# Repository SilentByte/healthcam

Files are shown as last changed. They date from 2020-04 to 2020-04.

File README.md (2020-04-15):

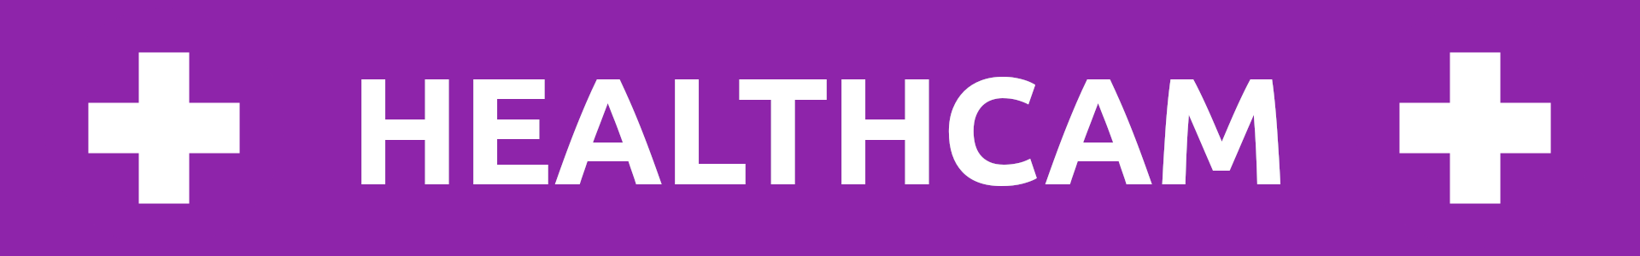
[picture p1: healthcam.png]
HealthCam


 &nbsp;
 &nbsp;


# HealthCam

In an effort to help with the currently ongoing COVID-19 health crisis, we have developed [HealthCam (healthcam.silentbyte.com)](https://www.healthcam.silentbyte.com/), a system based on the Raspberry Pi Camera and utilizing the [PPE Detector for Laboratory Safety](https://aws.amazon.com/marketplace/pp/prodview-b53upp27dnmzq) model provided by VITech Lab, which provides predictions for whether a person is wearing a mask or not. With this information, the system is able to automatically restrict door-access to sterile areas for people not wearing a mask in order to prevent the spread of infections.

Our submission contains two major components: the actual Raspberry Pi Camera with a door lock and the accompanying website to give
administrators access to manually flag detections as incorrect, and to view history of compliance, violation and manual
override events.

## AWS Services Used

| Service | Usage |
|---|---|
| Greengrass | Remote code deployment onto Raspberry Pi |
| API Gateway | Framework to publish and manage API |
| Lambda | Serverless functions to perform API actions|
| Amplify | Framework to build web applications |
| S3 | Object storage |
| RDS | Hosting of a PostgresSQL database |
| IAM | Management of AWS Permissions |
| Sagemaker Models Marketplace | Model for Mask detection |

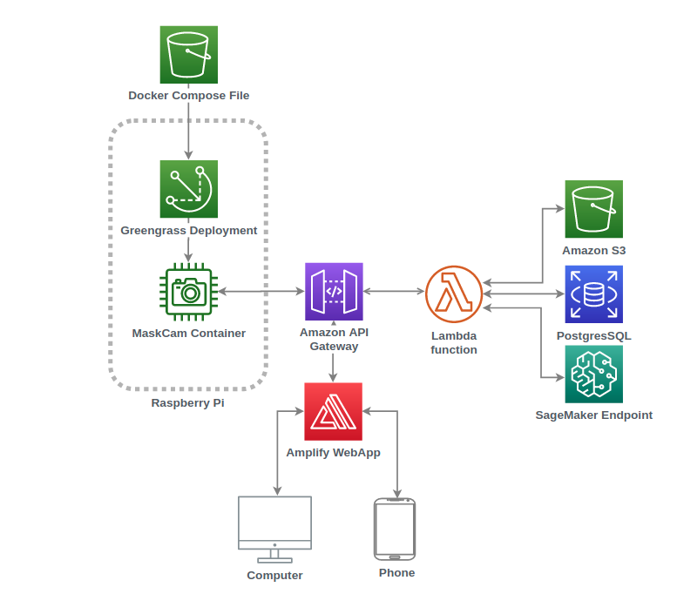
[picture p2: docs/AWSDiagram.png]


## Website
The website is powered by AWS Amplify and Vue/Vuetify, with all API calls made to AWS API Gateway. This website gives administrators the ability to manually flag detections as incorrect and view a history of compliance, violation and manual override events.

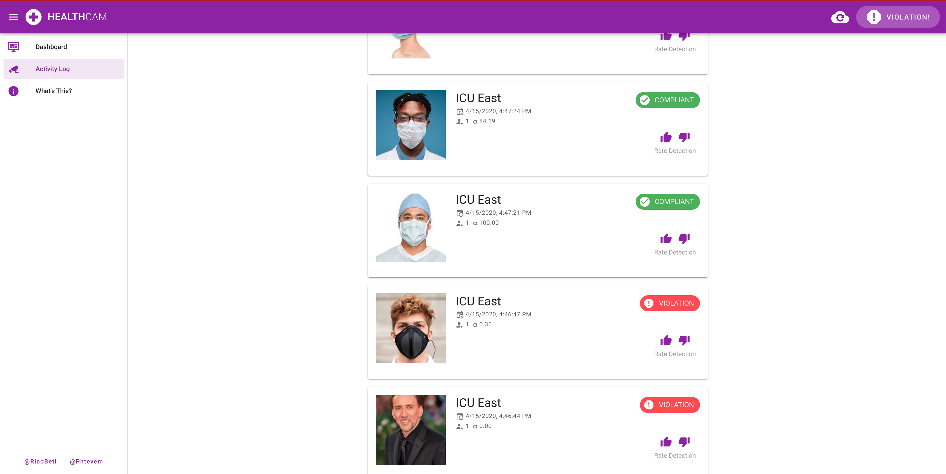
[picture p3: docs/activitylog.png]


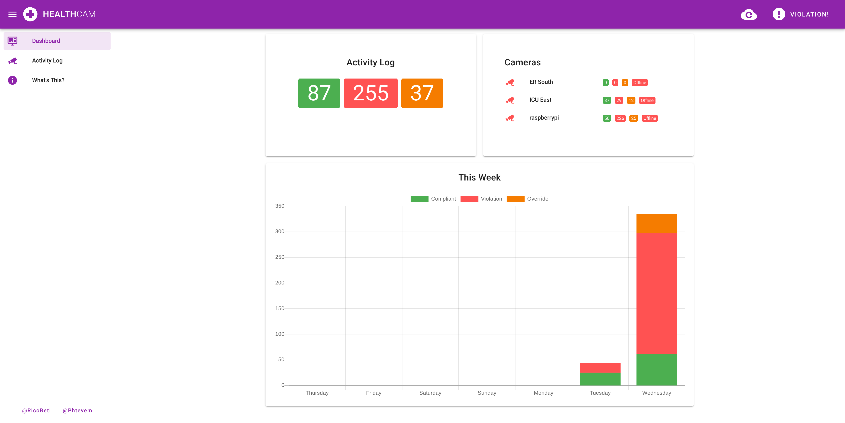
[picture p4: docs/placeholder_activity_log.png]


When the Rasbperry Pi detects movement in the frame, it sends an image along with some metadata to an API gateway endpoint.
A lambda function then picks this up, and first queries a Sagemaker endpoint created with the
[PPE Detector for Laboratory Safety](https://aws.amazon.com/marketplace/pp/prodview-b53upp27dnmzq).
The endpoint then returns information about the number of people in frame, the probability that each item is a person,
and the probability that they're wearing a mask. If there are people in the frame, then we take the lowest mask detected
probability, compare it to a user defined minimum probability to determine whether it's compliant or not and upload image
to a S3 bucket, a reference to where that image is along with the probability and number of people in frame to an RDS instance. Finally the Lambda sends a response back for whether the door should be opened or not. We have implemented a manual override button to open the door for emergency situations and in case of a false detection to guarantee that health works can continue to operate effectively and efficiently.

## Raspberry Pi
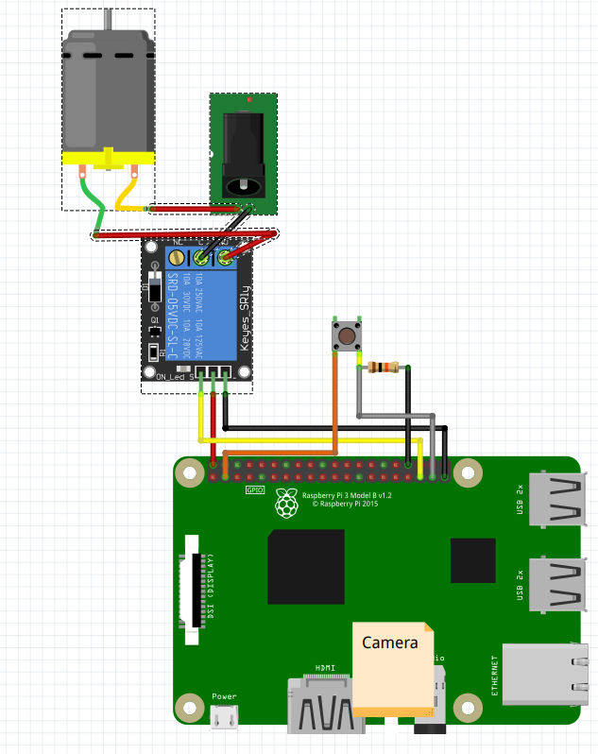
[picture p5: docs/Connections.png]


The Raspberry Pi system runs AWS Greengrass core. This allows the remote pushing of code and configurations through the AWS Greengrass Docker connector.
The main "Program" is installed as a python package and continually monitors for a percentage of pixels that have changed
by some user defined percentage. If this threshold has exceded then it will send the image it has captured through to
an AWS API Gateway endpoint, which will then do analysis on the image using the
[PPE Detector for Laboratory Safety](https://aws.amazon.com/marketplace/pp/prodview-b53upp27dnmzq) model, to determine
whether everyone in frame is wearing a mask.

If they are wearing a mask, then the Raspberry Pi Turns a GPIO pin connected to a relay to HIGH, which will actuate the
locking mechanism.

In the event of an emergency or false detection, there is a manual override button which will trigger an interrupt, immediately opening the
door, recording a picture and tagging the event as "override".

### Bill of Materials
| Item | Description |
| ---|---|
| [USB-C 5V 3A Power Supply](https://www.ebay.com.au/itm/Raspberry-Pi-4-4B-Power-Supply-Adapter-ON-OFF-Switch-USB-C-5V-3A-US-EU-Plug/303278828464) | Power for the Raspberry Pi |
| [12V 1A Power Supply](https://www.ebay.com.au/itm/AC-100-240V-Converter-Adapter-DC-12V-1A-12W-Power-Supply-AU-Plug-Wall-Charger/401648202115) | Power for the Lock Mechanism |
| [Electronic Latch Lock](https://www.ebay.com.au/itm/Electronic-Latch-Lock-Catch-Door-12V-Electro-magnet-Release-Solenoid-Slant-Slug/163889580407)| Lock Mechanism for Door |
| [5V relay](https://www.ebay.com.au/p/902676901) | Relay to isolate the lock power from the Pi|
| [Pi Camera V2](https://www.ebay.com.au/itm/Raspberry-Pi-Camera-Board-V2/323833141585) | Camera |
| [Dupont Line](https://www.ebay.com.au/itm/10-20-30CM-40PCS-Pin-Dupont-Wire-Line-Ribbon-M-F-M-M-F-F-Jumper-Cables-Arduino/274194461478) | Wiring |
| [Button](https://www.ebay.com.au/itm/10pcs-6x6x4-9mm-4pin-G89-Tactile-Push-Button-Micro-Switch-Self-Reset-Dip-Press/132693965284) | Press button for manual override of system |
| [10KΩ Resistor](https://www.ebay.com.au/itm/10pcs-1-4-Watt-0-25W-Metal-Film-Resistors-1-Full-Range-of-Values-0-to-10M/192581889373) | Pull down resistor for button |

## Setup

We've written extensive documentation on how to setup the aws resources and raspberry pi requirements to run this.

1. [Create Sagemaker Endpoint](setup/1_create_endpoint.md)

2. [Setup Frontend](setup/2_frontend.md)

3. [Setup Pi](setup/3_pi_setup.md)

## Challenges we ran into

### GreenGrass Setup
We wanted to drive our development and infrastructure without having to click through into the AWS UI to try to learn
how to better use the CLI and AWS SDKs. Because we hadn't used much Greengrass in the past it took us a while to properly
setup a Greengrass core and drive deployments without using the AWS UI. We'd recommend checking out this
[article](https://devopstar.com/2019/10/07/aws-iot-greengrass-cloudformation-raspberry-pi) if you're attempting greengrass and Raspberry Pi.
Unfortunately due to time constraints and last minute changes, one of the dependencies we introduced didn't work well with our docker container, so we had to deploy via Pip instead.

### IAM
We don't work with AWS a lot and we wanted to avoid our bad behaviours of the past with allow *, so learning how to properly apply the required AWS policies to roles specific to their task was an interesting experience. We've identified a lot of cases where we could have done a lot better, so hopefully we'll fix those up.

### OpenCV and Raspberry Pi
Some changes to OpenCV (used for detecting image differences) in November broke a few packages. Thankfully
[Adrian Rosebrock](https://www.pyimagesearch.com/2019/09/16/install-opencv-4-on-raspberry-pi-4-and-raspbian-buster/)
has updated his blog with steps around this. In retrospect given the problems we had, it would probably have been worth
doing the pixel change detection in numpy instead of using such a heavy library to do it for us.

### Models Limitations
Currently, the SageMaker model seems to have a limitation in that it doesn't properly detect non-white/blue masks.

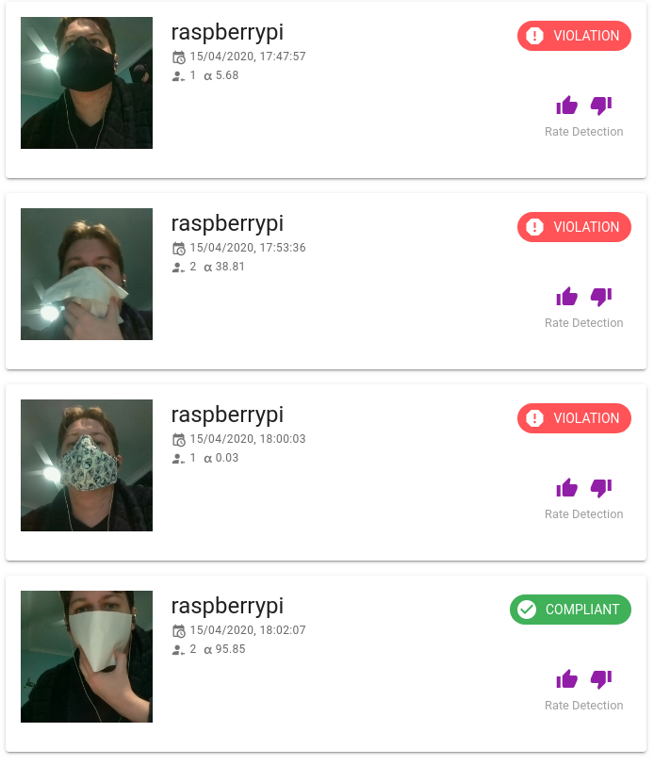
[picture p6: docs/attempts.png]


## What We Learnt

This hackathon gave us the chance to once again dive into Amazon Web Services. New services for us this time were AWS IoT Greengrass and AWS Amplify, which are now part of our toolbox.

## What's Next
### Authentication
Currently there is no Authentication on the API gateway or website. This is something that's probably required if anyone
is going to use this, so it would be well worth us putting in the effort to get this in. We would probably want to use
AWS Cognitio with Federated Identities to do manage credentials.

### Cloudformation Deployments
Because we used two different frameworks (Serverless Framework and AWS Amplify) we didn't really have a single deployment pipeline.
Ideally we'd fully embrace Infrastructure as a Service and use Cloudformation to manage all of our cloud resources.

### Proper Deployment Pipleine (CICD)
One of the things that slowed us down a bit was the lack of a proper deployment pipeline which occasionally slowed us down:

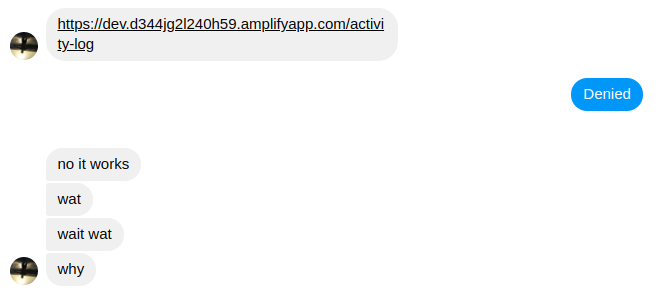
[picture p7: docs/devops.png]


We would probably want to implement proper Continuous Integration/Continuous Deployment to avoid us
having to push code manually and to make sure that we have some automated tests running against our code once deployed to AWS.

### Proper Bootstrap Script for Raspberry Pi
Currently the setup of the Raspberry Pi and Greengrass is a bit more complicated than it needs to be. Based on the steps,
it should be easy enough to set up a proper bootstrap script to setup the pi ready for greengrass deployments.

## Thanks
There were a few resources that we found invaluable while we were making this
* [Setting up Greengrass on a Raspberry Pi](https://devopstar.com/2019/10/07/aws-iot-greengrass-cloudformation-raspberry-pi) was a great into to Greengrass.
* [Accessing the Raspberry Pi Camera](https://www.pyimagesearch.com/2015/03/30/accessing-the-raspberry-pi-camera-with-opencv-and-python/)
had some useful tips on how to poll the Pi Camera a lot faster than I was previously polling it.
* [Install OpenCV4 on Raspberry Pi](https://www.pyimagesearch.com/2019/09/16/install-opencv-4-on-raspberry-pi-4-and-raspbian-buster/)
* [Launch RDS with AWS CLI](https://www.mydatahack.com/how-to-launch-postgres-rds-with-aws-command-line-interface-cli/)
* [raspi-config noint commands](https://github.com/l10n-tw/rc_gui/blob/master/src/rc_gui.c#L50-L100) very useful for enabling things via cli
* [AWS Docker Connector](https://docs.aws.amazon.com/greengrass/latest/developerguide/docker-app-connector.html) information on the greengrass docker connector

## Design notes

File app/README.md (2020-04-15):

HealthCam

 &nbsp;
 &nbsp;


# HealthCam App

This part of the repository is representing the front-end of the HealthCam app and is based on Vue and Vuetify.

## Development

In order to start development on this project, follow the steps below:

*   Ensure that the AWS Lambda-based back-end service is running locally on port 8888. You can find instructions in the `./lambdas` folder in this repository.

*   Install app dependencies:
    ```bash
    $ cd app
    $ npm install
    ```

*   Start app in development mode:
    ```bash
    $ npm run dev
    ```

    At this point, the app should have been bundled and a development server should have been started on port 8080.

## Deployment

This project is powered by [AWS Amplify](https://aws-amplify.github.io/) and requires you to sign up for an AWS account if you choose to deploy using that service.

*   Ensure that the AWS Lambda-based back-end has been deployed. You can find instructions in the `./lambdas` folder in this repository.

*   Create the file `.env.development.local` in the `./app/` folder and set the endpoint URL to the base URL to which the Lambda service has been deployed:

    ```
    VUE_APP_API_URL=https://your-lambda-url.execute-api.us-east-1.amazonaws.com/dev
    ```

*   Configure your AWS Amplify project:
    ```bash
    $ cd app
    $ npm install -g @aws-amplify/cli
    $ amplify configure
    ```

*   Publish the HealthCam app on AWS Amplify:
    ```bash
    $ amplify publish
    ```

If the deployment has been successful, a publicly accessible URL will be displayed and HealthCam is now up and running. :-)

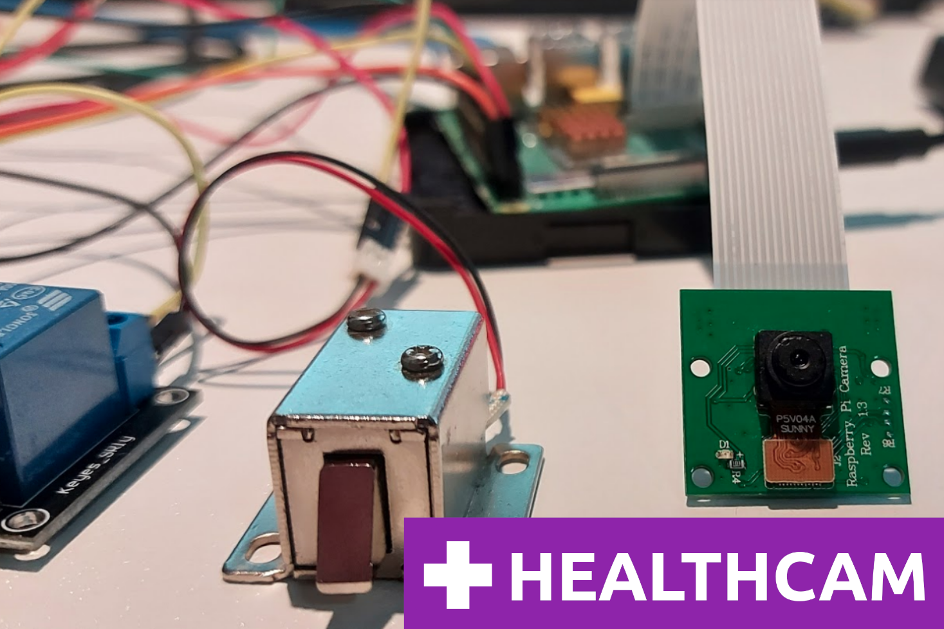
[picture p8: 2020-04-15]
docs/project.png

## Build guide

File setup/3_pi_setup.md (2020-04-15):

# Set up Pi
[Download Raspbian Buster lite](https://downloads.raspberrypi.org/raspbian_lite_latest) and extract it

Use [Etcher](https://www.balena.io/etcher/) to install the Rasbpian ISO to your SD Card.

On your SD card go to ```boot``` and add a new file called ```ssh```. This will enable SSH on boot.

You should now be able to put your SD card 

Check that your raspberry Pi is online with ```ping raspberrypi.local```
```
PING raspberrypi.local (192.168.0.167) 56(84) bytes of data.
64 bytes from raspberrypi.modem (192.168.0.167): icmp_seq=1 ttl=64 time=0.889 m
```

SSH into the Raspberry Pi

```
# Enable GPIO and Camera
sudo apt-get update
sudo apt-get install pigpio -y
sudo raspi-config nonint do_camera 1
sudo raspi-config nonint do_rgpio 1
# Install docker
sudo apt install docker docker-compose -y
# Setup docker group for current user and green grass user
sudo adduser -m ggc_user
sudo addgroup --system ggc_group
sudo groupadd docker
sudo usermod -aG docker pi
sudo usermod -aG docker ggc_user
# setup opencv (for devel purposes).
sudo apt install libtiff-dev libjpeg8-dev libpng12-dev build-essential  -y
sudo apt install python3-pyqt5 libqtgui4 libjasper-dev libatlas-base-dev libatlas-base-dev libgtk2.0-dev libtbb-dev qt5-default -y
sudo apt install python3-opencv -y
```

Install the MaskCam package
```
git clone git@github.com:SilentByte/healthcam.git
cd healthcam/Picode
pip3 install -r requirements.txt
pip3 install -e .
```
You should now be able to run ```MaskCam``` to access settings 
```zsh
pi@raspberrypi:~ $ MaskCam --help
Usage: MaskCam [OPTIONS] COMMAND [ARGS]...

Options:
  --camera_number INTEGER       Raspberry Pi camera number according to https:
                                //picamera.readthedocs.io/en/release-1.13/api_
                                camera.html#picamera, Default: 0

  --camera_invert BOOLEAN       Vertical invert camera, Default: True
  --device_name TEXT            Device Name, Default: raspberrypi
  --minimum_difference INTEGER  Minimum difference between frames to send,
                                Default: 50

  --api_gateway TEXT            AWS API Gateway Endpoint, Default:
                                https://m5k4jhx1ka.execute-api.us-
                                east-1.amazonaws.com/dev/

  -v, --verbose                 Verbosity. More v, more verbose. Eg -vvv
  --door_button INTEGER         Pin that the override button is connected to,
                                Default: 37

  --door_pin INTEGER            Pin the door latch is connected to, Default:
                                35

  --opening_time INTEGER        Time to open door in seconds., Default: 5
  --help                        Show this message and exit.

Commands:
  to_aws
  to_file
  to_stdout
```
For most cases if you run ```MaskCam --api_gateway {YOUR GATWAY URL} to_aws``` you should be fine.

#Setup Greengrass
# Setup Roles
## Bootstrap Role
Create the "Bootstrap" role which will install your greengrass components onto your raspberry pi.

get your ARN with ```aws iam get-role --role-name Greengrass_ServiceRole ```
```
aws greengrass associate-service-role-to-account --role-arn {YOUR_ROLE} --region us-east-1

```
Create a "boostrap" user that will be creating your greengrass core deployment
```
aws iam create-user --user-name bootstrapuser
aws iam create-access-key --user-name bootstrapuser
aws iam attach-user-policy --user-name bootstrapuser --policy-arn arn:aws:iam::aws:policy/AWSGreengrassFullAccess
aws iam attach-user-policy --user-name bootstrapuser --policy-arn arn:aws:iam::aws:policy/AWSIoTConfigAccess
aws iam attach-user-policy --user-name bootstrapuser --policy-arn arn:aws:iam::aws:policy/IAMFullAccess
```

## Greengrass Service Role
Create your Greengrass Service Role to allow your greengrass group to run.
Check if you have a previous service role
```
aws greengrass get-service-role-for-account --region us-east-1
```
Diasassociate it
```
aws greengrass disassociate-service-role-from-account --region region
```
Give your role the required permissions
```
aws iam create-role --role-name Greengrass_ServiceRole --assume-role-policy-document '{
  "Version": "2012-10-17",
  "Statement": [
    {
      "Effect": "Allow",
      "Principal": {
        "Service": "greengrass.amazonaws.com"
      },
      "Action": "sts:AssumeRole"
    }
  ]
}'
aws iam attach-role-policy --role-name Greengrass_ServiceRole --policy-arn arn:aws:iam::aws:policy/service-role/AWSGreengrassResourceAccessRolePolicy
```
Download greengrass setup
```
wget -q -O ./gg-device-setup-latest.sh https://d1onfpft10uf5o.cloudfront.net/greengrass-device-setup/downloads/gg-device-setup-latest.sh && chmod +x ./gg-device-setup-latest.sh
```
Input the aws-access-key-id and aws-secret-access-key from ```aws iam create-access-key --user-name bootstrapuser```. This will createa a group-name and core-name with the serial number of your raspberry pi.
```
sudo ./gg-device-setup-latest.sh bootstrap-greengrass \
--aws-access-key-id {} \
--aws-secret-access-key {} \
--region us-east-1 \
--group-name $(cat /proc/cpuinfo | grep Serial | cut -d ' ' -f 2) \
--core-name $(cat /proc/cpuinfo | grep Serial | cut -d ' ' -f 2)

```

```
[GreengrassDeviceSetup] A reboot is required to make cgroups configuration change effective.
You must reboot your device manually and then restart GreengrassDeviceSetup.
```

```sudo reboot```
re run the previous ```./gg-device-setup-latest.sh``` command. This time you'll get
```
Do you want to reuse the configuration from your previous session? Enter 'yes' to reuse the configuration or 'no' to restart the installation.
```
yes

```
You can now use AWS IoT Console to manage your Greengrass group.
```

attach the service role to your docker

```
aws greengrass list-groups
```
get your group name and attach your service role with it
```
get your ARN with ```aws iam get-role --role-name Greengrass_ServiceRole ```
```
Associate this role with your greengrass group
```
aws greengrass associate-role-to-group --group-id {YOUR_GROUP_ID} --role-arn {YOUR_ROLE_ARN}
```
Confirm with
```
aws greengrass get-associated-role --group-id {YOUR_GROUP_ID}
```

# Deploy your container
Replace YOUR_BUCKET_NAME and YOUR_DOCKER_COMPOSE_FILE_NAME with what you created in step 1.
```
aws greengrass create-connector-definition --name MyGreengrassConnectors --initial-version '{
    "Connectors": [
        {
            "Id": "MyDockerAppplicationDeploymentConnector",
            "ConnectorArn": "arn:aws:greengrass:region::/connectors/DockerApplicationDeployment/versions/2",
            "Parameters": {
                "DockerComposeFileS3Bucket": "{YOUR_BUCKET_NAME}",
                "DockerComposeFileS3Key": "{YOUR_DOCKER_COMPOSE_FILE_NAME}",
                "DockerComposeFileDestinationPath": "/home/ggc_user",
                "ForceDeploy": "True"
            }
        }
    ]
}'
```
you should now be able to create a new deployment via the AWS console

# References
[Enable SSH on boot](https://www.raspberrypi.org/forums/viewtopic.php?t=129727)

[raspi-config noint commands](https://github.com/l10n-tw/rc_gui/blob/master/src/rc_gui.c#L50-L100)

[Greengrass quick setup](https://docs.aws.amazon.com/greengrass/latest/developerguide/quick-start.html)

[Connector](https://docs.aws.amazon.com/greengrass/latest/developerguide/docker-app-connector.html)
[Install OpenCV4](https://www.learnopencv.com/install-opencv-4-on-raspberry-pi/)

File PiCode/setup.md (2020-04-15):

```
model_package=arn:aws:sagemaker:us-east-1:865070037744:model-package/sassy-atermis-05-693a26662ad851a0e47bf8146e940526
aws iam list-roles --query 'Roles[?AssumeRolePolicyDocument.Statement[?Principal.Service==`sagemaker.amazonaws.com`]].{Arn:Arn,RoleName:RoleName,Principal:AssumeRolePolicyDocument.Statement[0].Principal.Service}'
aws iam get-role --query 'Role.{Arn:Arn}' --role-name <role-name>
execution_role_arn=<iam-role-arn>
instance_type=ml.p2.xlarge
supported_instance_types=(ml.p2.xlarge)

aws sagemaker create-model --model-name sample-model-51119791-78EE-457C-AA7F-679C5CE281DE-1 --execution-role-arn ${execution_role_arn} --primary-container ModelPackageName=${model_package} --enable-network-isolation --region us-east-1
aws sagemaker create-endpoint-config --endpoint-config-name sample-endpointcfg-51119791-78EE-457C-AA7F-679C5CE281DE-1 --production-variants VariantName=variant-1,ModelName=sample-model-51119791-78EE-457C-AA7F-679C5CE281DE-1,InstanceType=${instance_type},InitialInstanceCount=1 --region us-east-1
aws sagemaker create-endpoint --endpoint-name sample-endpoint-51119791-78EE-457C-AA7F-679C5CE281DE-1 --endpoint-config-name sample-endpointcfg-51119791-78EE-457C-AA7F-679C5CE281DE-1 --region us-east-1
aws sagemaker describe-endpoint --endpoint-name sample-endpoint-51119791-78EE-457C-AA7F-679C5CE281DE-1 --region us-east-1

```

```
sudo apt install python3 python3-pip
pip3 install -r requirements.txt
sudo apt-get install python-opencv
pip install opencv-contrib-python==4.1.0.25
sudo apt-get install python-opencv
sudo apt install libatlas3-base libwebp6 libtiff5 libjasper1 libilmbase12 libopenexr22 libilmbase12 libgstreamer1.0-0 libavcodec57 libavformat57 libavutil55 libswscale4 libqtgui4 libqt4-test libqtcore4
sudo apt-get install libjpeg-dev libtiff5-dev libjasper-dev libpng12-dev -y
sudo apt install libqt4-test

sudo apt-get install libatlas-base-dev 

sudo apt-get install libjasper-dev 

sudo apt-get install libqtgui4 

sudo apt-get install python3-pyqt5 

sudo apt install libqt4-test

sudo apt install python3-pyqt5 libqtgui4 libjasper-dev libatlas-base-dev -y
sudo apt install python3-opencv -y

sudo apt-get install libavcodec-dev libavformat-dev libswscale-dev libv4l-dev -y
sudo apt-get install libxvidcore-dev libx264-dev -y
sudo apt-get install libgtk2.0-dev libgtk-3-dev -y
sudo apt-get install libatlas-base-dev gfortran -y
sudo apt-get install libqtgui4 python3-pyqt5 libjasper-dev libatlas-base-dev
sudo apt-get install 

```
# Sagemaker
```
https://aws.amazon.com/marketplace/pp/prodview-3dr4kos6pq5cq?ref_=ml_hackathon
https://aws.amazon.com/marketplace/ai/configuration?productId=9883feb9-7190-4372-8eaf-fd5a95126daa
arn:aws:sagemaker:us-east-2:057799348421:model-package/sassy-anthropos-05-28e3401e81bd6a58dd876017dfc821db

```

# request limits 
https://docs.aws.amazon.com/general/latest/gr/sagemaker.html
ml.p3.2xlarge instances	
https://udacity.zendesk.com/hc/en-us/articles/360037696812-How-do-I-request-a-limit-increase-for-my-p2-xlarge-instance-

```
https://docs.aws.amazon.com/sagemaker/latest/dg/appendix.html
```

sudo apt-get install libatlas-base-dev

References

https://www.pyimagesearch.com/2015/03/30/accessing-the-raspberry-pi-camera-with-opencv-and-python/

https://www.pyimagesearch.com/2019/03/25/building-a-raspberry-pi-security-camera-with-opencv/

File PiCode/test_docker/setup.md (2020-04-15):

```
docker build . -t "foo:bar"
docker run --device=/dev/vchiq foo:bar
```
Should get the output
```zsh
Recording I guess?
['/home/test.mjpeg', '/home/foo.jpeg']
18069702
142834
```

Showing that you're able to write a video and a file.

I'll point out that currently I'm seeing this generally 1/3 times I try to run the container
```zsh
mmal: mmal_vc_port_enable: failed to enable port vc.null_sink:in:0(OPQV): ENOSPC
mmal: mmal_port_enable: failed to enable connected port (vc.null_sink:in:0(OPQV))0xbd2c50 (ENOSPC)
mmal: mmal_connection_enable: output port couldn't be enabled
Traceback (most recent call last):
  File "test.py", line 8, in <module>
    cam = PiCamera(camera_num=0)
  File "/usr/lib/python3/dist-packages/picamera/camera.py", line 433, in __init__
    self._init_preview()
  File "/usr/lib/python3/dist-packages/picamera/camera.py", line 513, in _init_preview
    self, self._camera.outputs[self.CAMERA_PREVIEW_PORT])
  File "/usr/lib/python3/dist-packages/picamera/renderers.py", line 558, in __init__
    self.renderer.inputs[0].connect(source).enable()
  File "/usr/lib/python3/dist-packages/picamera/mmalobj.py", line 2212, in enable
    prefix="Failed to enable connection")
  File "/usr/lib/python3/dist-packages/picamera/exc.py", line 184, in mmal_check
    raise PiCameraMMALError(status, prefix)
picamera.exc.PiCameraMMALError: Failed to enable connection: Out of resources
```
Would strongly suggest coding with the expectation that the first N times you try to get the camera, it fails and add a try loop in there.

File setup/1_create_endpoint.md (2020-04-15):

# Request AWS Limits
Before you'll be able to create the model you'll need to request your service limits to be increased, to allow you to
 host a ```ml.p3.2xlarge``` SageMaker hosting instance.
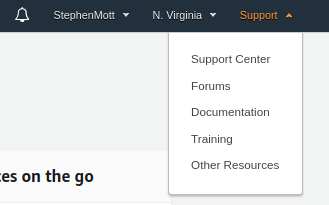
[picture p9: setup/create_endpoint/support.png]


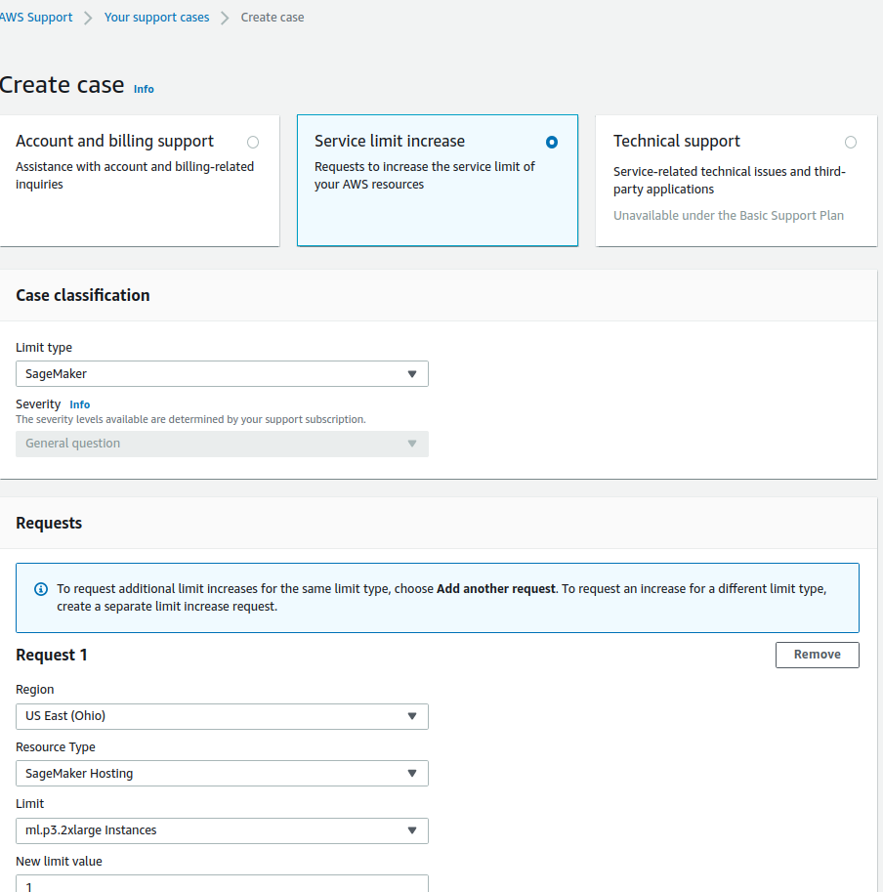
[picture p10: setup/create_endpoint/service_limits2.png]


# Subscribe to model
Subscribe to the [PPE Detector for Worker Safety](https://aws.amazon.com/marketplace/pp/prodview-6gvzwuebead3o?ref_=_ml_hackathon)
. At time of writing there is a 30 day trial for this.

# Create required roles
```
aws iam create-role --role-name SagemakerRole --assume-role-policy-document '{                                                                
  "Version": "2012-10-17",
  "Statement": [
    {
      "Effect": "Allow",
      "Principal": {
        "Service": "sagemaker.amazonaws.com"
      },
      "Action": "sts:AssumeRole"
    }
  ]
}'
aws iam attach-role-policy --role-name SagemakerRole --policy-arn arn:aws:iam::aws:policy/AmazonSageMakerFullAccess
Get ARN
aws iam get-role --role-name SagemakerRole | grep Arn

export model_name=YOUR_MODEL_NAME
export endpoint_name=YOUR_ENDPOINT_NAME

```

# Setup Model Endpoint.
```
aws sagemaker create-model --model-name ${model_name} --execution-role-arn 'arn:aws:iam::811908451910:role/SagemakerRole' --primary-container ModelPackageName='arn:aws:sagemaker:us-east-1:865070037744:model-package/vitechlab-ppe-lab-model-v1-1-480cb3fc5bd97e9bf1e213cca498bbc4' --region us-east-1
```
save the returned arn

Note it will need to be in the format ```^[a-zA-Z0-9](-*[a-zA-Z0-9])*```
```
aws sagemaker create-endpoint-config --endpoint-config-name my-endpoint --production-variants VariantName=variant-1,ModelName=${model_name},InstanceType=ml.p3.2xlarge,InitialInstanceCount=1 --region us-east-1
aws sagemaker create-endpoint --endpoint-name ${model_name} --endpoint-config-name my-endpoint --region us-east-1
```

Check endpoint
```
aws sagemaker describe-endpoint --endpoint-name ${model_name} --region us-east-1
```

You'll need to wait until your endpoint moves from ```creating``` before using it.
Save your endpoint name, you'll need it later.
```

aws sagemaker delete-endpoint --endpoint-name ${model_name} --region us-east-1

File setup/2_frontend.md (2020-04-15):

# Create RDS DB
```
aws rds create-db-instance 
--engine postgres \
--db-instance-identifier PUT_A_NAME_IN_HERE \
--allocated-storage 20 \
--db-instance-class db.t2.micro \
--publicly-accessible 
--master-username PUT_USERNAME_HERE \
--master-user-password PUT_PASSWORD_HERE \
--backup-retention-period 3

```
Check your database with  ```aws rds describe-db-instances --region us-east-1| grep 'DBInstanceIdentifier":' -A 7``` and wait until the field ```DBInstanceStatus``` becomes "available".

After this you should be able to connect to this publicly accessible data, I suggest [dbeaver](https://dbeaver.io/download/) if you don't already have a favourite SQL tool.

Make sure to record your Endpoint and username/password for later steps

# Create S3 Bucket
To keep the S3 bucket external to the deployments we've created it separately via the AWS CLI
```
aws s3a create-bucket --bucket YOUR_BUCKET_NAME_HERE --region us-east-1
```

## Lambdas

### Development

*   Create a Python virtual environment and install lambda dependencies:
    ```bash
    $ cd lambdas
    $ virtualenv --python python3 venv
    $ source venv/bin/activate
    $ pip install -r requirements.txt
    $ npm install
    ```

*   Set lambda environment variables by creating the file `.env.development` with the following variables:
    ```bash
    DEBUG=True
    PRODUCTION=False
    # Bucket name and a prefix for the photos
    PHOTO_BUCKET_NAME=S3_BUCKET_NAME
    PHOTO_KEY_PREFIX=healthcam/
    # Database info from your RDS instance
    DB_HOST=YOUR_DATABASE_HOST
    DB_PORT=YOUR_DATABASE_PORT
    DB_NAME=YOUR_DATABASE_NAME
    DB_USER=YOUR_DATABASE_USER
    DB_PASSWORD=YOUR_DATABASE_PASSWORD
    # Your sagemaker endpoint name created in step 1
    SAGEMAKER_ENDPOINT=
    ```

*   Start lambdas in development mode:
    ```bash
    $ npm run dev
    ```

### Deployment

To deploy the lambdas, follow the steps above and then run:

*   Start lambdas in development mode:
    ```bash
    $ npm run deploy
    ```

## Website

### Development

In order to start development on this project, follow the steps below:

*   Ensure that the AWS Lambda-based back-end service is running locally on port 8888.

*   Install app dependencies:
    ```bash
    $ cd app
    $ npm install
    ```

*   Start app in development mode:
    ```bash
    $ npm run dev
    ```

    At this point, the app should have been bundled and a development server should have been started on port 8080.

### Deployment

This project is powered by [AWS Amplify](https://aws-amplify.github.io/) and requires you to sign up for an AWS account if you choose to deploy using that service.

*   Ensure that the AWS Lambda-based back-end has been deployed.

*   Create the file `.env.development.local` in the `./app/` folder and set the endpoint URL to the base URL to which the Lambda service has been deployed:

    ```
    VUE_APP_API_URL=https://your-lambda-url.execute-api.us-east-1.amazonaws.com/dev
    ```

*   Configure your AWS Amplify project:
    ```bash
    $ cd app
    $ npm install -g @aws-amplify/cli
    $ amplify configure
    ```

*   Publish the HealthCam app on AWS Amplify:
    ```bash
    $ amplify publish
    ```

If the deployment has been successful, a publicly accessible URL will be displayed and HealthCam is now up and running. :-)

# References 
[Launch RDS with AWS CLI](https://www.mydatahack.com/how-to-launch-postgres-rds-with-aws-command-line-interface-cli/)

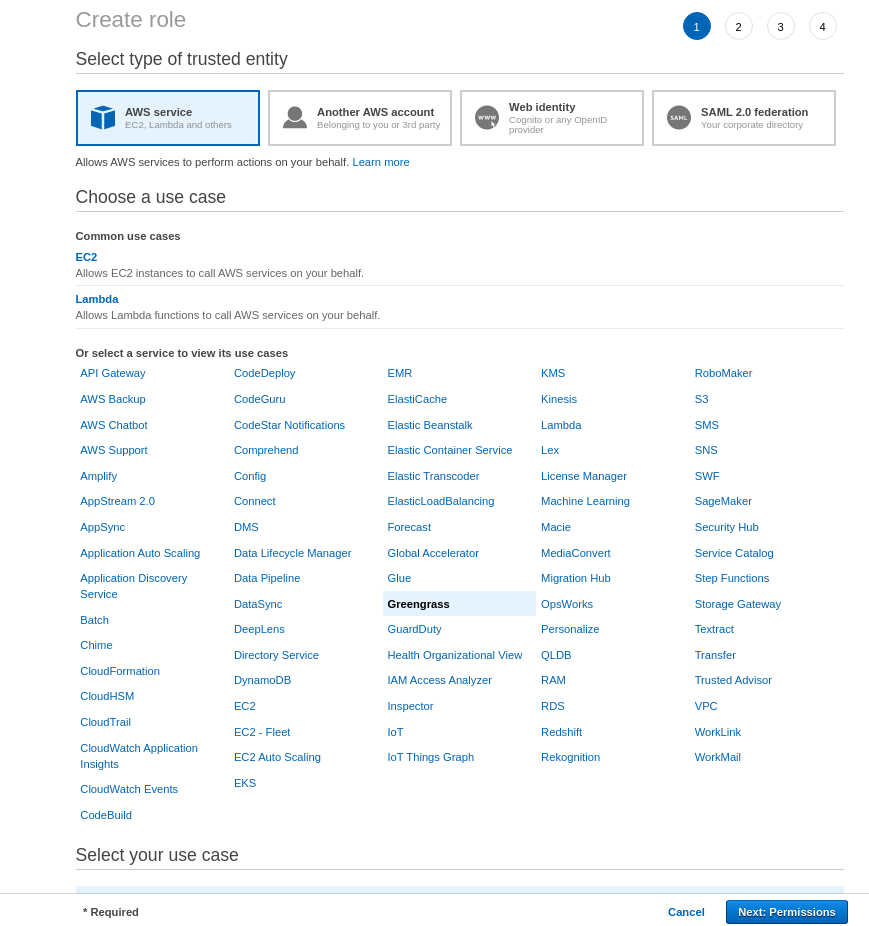
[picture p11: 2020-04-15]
setup/docs/pi_setup/create_role_gg.png

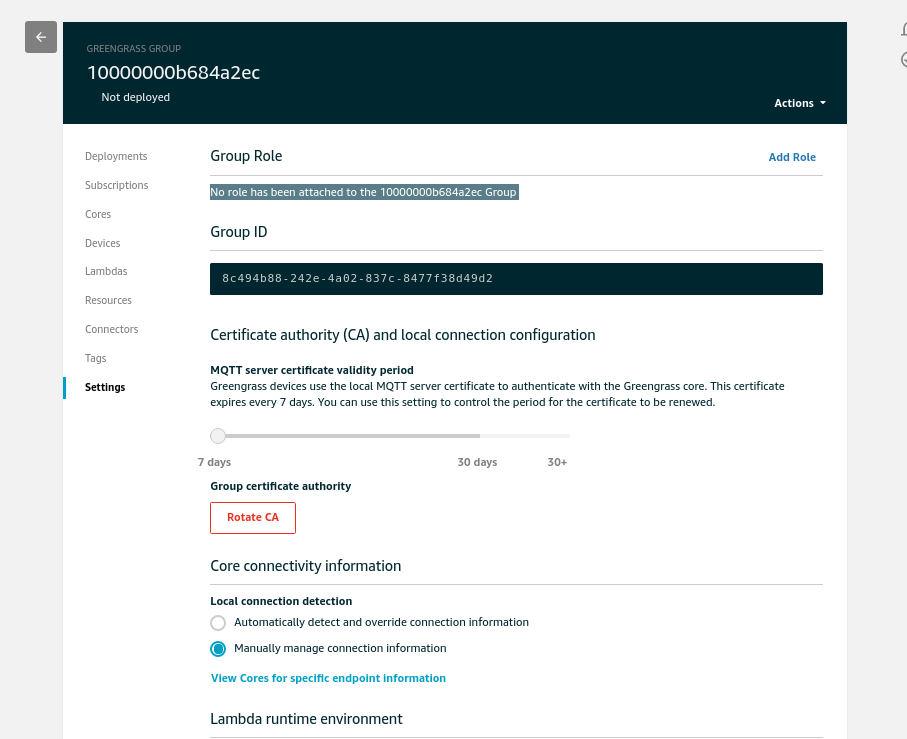
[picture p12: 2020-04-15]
setup/docs/pi_setup/add_role.png

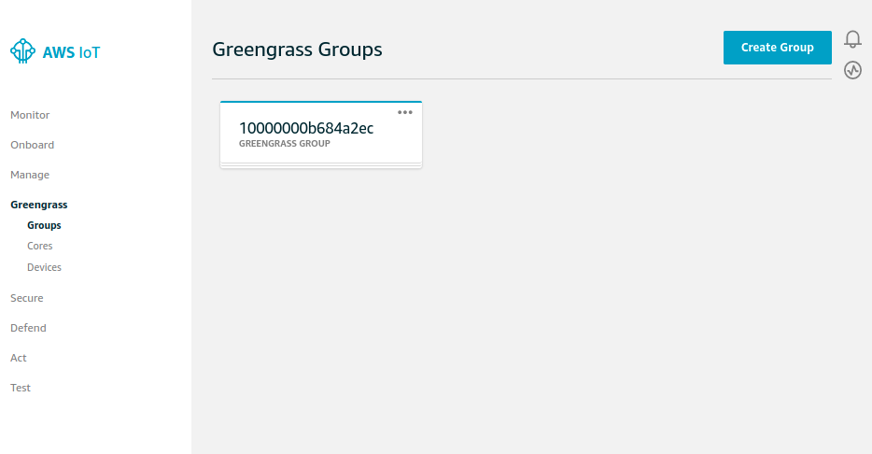
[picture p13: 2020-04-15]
setup/docs/pi_setup/groups.png

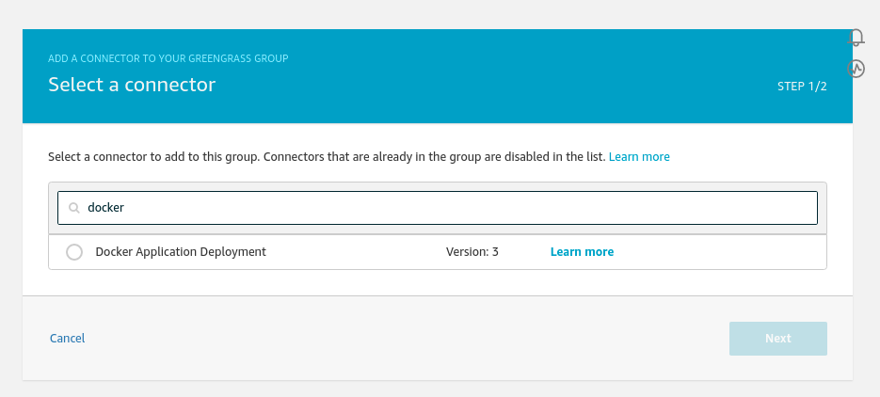
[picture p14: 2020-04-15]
setup/docs/pi_setup/dockerconnector.png

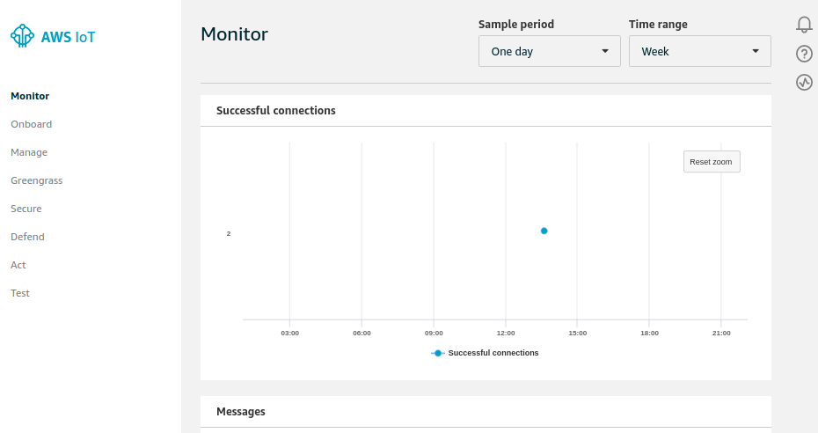
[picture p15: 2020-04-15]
setup/docs/pi_setup/success_connection.png

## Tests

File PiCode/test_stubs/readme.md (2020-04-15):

Initial tests to allow testing of API gateway to
1. Standardise the output
2. Test API gateway before Pi code is done
3. Make it waaay easier to test the API Gateway

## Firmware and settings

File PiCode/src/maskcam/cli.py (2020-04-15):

import click
from maskcam.settings import *
from pathlib import Path
from attentive import quitevent
from json import dumps, JSONDecodeError
from maskcam.common_fns import data_generator, session_with_retry_policy, set_verbosity
from base64 import b64encode
import RPi.GPIO as GPIO
from time import time, sleep
from maskcam.settings import DOOR_OUT_PIN, DOOR_OVERRIDE_BUTTON, OPEN_TIME, DEVICE_NAME
from logging import getLogger
from maskcam.common_fns import session_with_retry_policy, open_door, get_serial_number, Pinger, generate_payload
import pytz
from datetime import datetime
from PIL import Image as PIL_IMAGE
from maskcam.camera import Camera

logger = getLogger(__name__)

GPIO.setmode(GPIO.BOARD)


class ConfigObject:
    def __init__(self):
        pass


config_class = click.make_pass_decorator(ConfigObject, ensure=True)


# todo proper knobs on some of these
@click.group()
@click.option('--camera_number', default=CAMERA_NUMBER(), help=CAMERA_NUMBER.help(), type=int)
@click.option('--camera_invert', default=INVERT_CAMERA(), help=INVERT_CAMERA.help(), type=bool)
@click.option('--device_name', default=DEVICE_NAME(), help=DEVICE_NAME.help(), type=str)
@click.option('--minimum_difference', default=MIN_PERCENTAGE_DIFF(), help=MIN_PERCENTAGE_DIFF.help(), type=int)
@click.option('--api_gateway', default=AWS_API_GATEWAY(), help=AWS_API_GATEWAY.help(), type=str)
@click.option('-v', '--verbose', default=4, count=True, help="Verbosity. More v, more verbose. Eg -vvv")
@click.option('--door_button', default=DOOR_OVERRIDE_BUTTON(), help=DOOR_OVERRIDE_BUTTON.help())
@click.option('--door_pin', default=DOOR_OUT_PIN(), help=DOOR_OUT_PIN.help())
@click.option('--opening_time', default=OPEN_TIME(), help=OPEN_TIME.help())
@config_class
def cli(config, camera_number, camera_invert, device_name, minimum_difference, api_gateway, verbose, door_button,
        door_pin, opening_time):
    GPIO.setup(door_button, GPIO.IN, pull_up_down=GPIO.PUD_DOWN)
    GPIO.setup(door_pin, GPIO.OUT)

    # setup logging
    set_verbosity(verbose)
    # Set up generator
    config.camera = Camera(invert=camera_invert, camera_num=camera_number)
    config.camera.start_polling()
    gen = data_generator(Cam=config.camera, threshold=minimum_difference)
    config.camera_num = camera_number
    config.invert_cam = camera_invert
    config.device_name = device_name
    config.min_diff = minimum_difference
    config.gateway_url = api_gateway
    config.generator = gen
    config.door_pin = door_pin
    config.api_gateway = api_gateway
    config.open_time = opening_time

    callback_fn = lambda x: open_door(config, override=True)
    GPIO.add_event_detect(door_button, GPIO.RISING, callback=callback_fn, bouncetime=1000)


@cli.command("to_stdout")
@config_class
def to_stdout(config, file_path):
    # Friendly debugging command.
    serial = get_serial_number()
    while not quitevent.is_set():
        for image in config.generator:
            with session_with_retry_policy() as Session:
                data = generate_payload(config=config, image=image)
                try:
                    response = Session.post(f"{config.gateway_url}upload", data=dumps(data))
                    print(response.content)
                except Exception as e:
                    logger.warning(f"got error {e} with payload {data} continuing anyway")
                    pass


@cli.command("to_file")
@click.option("--file_path", default="/tmp/data", help="Directory to save predictions to", type=str)
@config_class
def to_file(config, file_path):
    # Friendly debugging command.
    serial = get_serial_number()
    image_int = 0
    file_path = Path(file_path)
    if file_path.is_file():
        raise FileExistsError(f"Inputted directory {file_path.absolute()} is a file")
    if not file_path.exists():
        file_path.mkdir(parents=True)
    while not quitevent.is_set():
        for image in config.generator:
            image_int += 1
            PIL_IMAGE.fromarray(image).save(f'{file_path.absolute()}/{image_int}.jpeg')
            with session_with_retry_policy() as Session:
                data = generate_payload(config=config, image=image)
                try:
                    response = Session.post(f"{config.gateway_url}upload", data=dumps(data))
                    with open(f"{file_path.absolute()}/{image_int}.txt", 'wb') as fp:
                        fp.write(response.content.decode('utf-8'))

                except Exception as e:
                    logger.warning(f"got error {e} with payload {data} continuing anyway")
                    pass


@cli.command("to_aws")
@config_class
def to_aws(config):
    serial = get_serial_number()
    ping = Pinger(gateway_URL=f"{config.gateway_url}ping", device_name=config.device_name)
    ping.start()
    while not quitevent.is_set():
        for image in config.generator:
            # We got an event where the camera was diffed.
            with session_with_retry_policy() as Session:
                # Not strictly correct, not a binary image.
                data = generate_payload(config=config, image=image)
                response = Session.post(f"{config.gateway_url}upload", data=dumps(data))
                try:
                    response.raise_for_status()
                except Exception as e:
                    # If we get a non 200 status code, try again
                    logger.debug(e)
                    logger.warning(f"got {response.status_code} \n for payload {data} \n with data {response.content}")
                    continue
                try:
                    response = response.json()
                    if len(response) == 0:
                        logger.info("no people in frame")
                        pass
                    else:
                        if response.get('activity') == 'compliant':
                            logger.info("Opening door. Thanks for wearing a mask.")
                            open_door(config, override=False)
                        else:
                            logger.info(
                                f"I see {len(response['sagemaker_response'])} people and one of you isn't wearing a mask.")
                            logger.info("Wear a mask. I'm not opening the door until you do.")
                            pass
                # If we can't decode this to JSON then it's an invalid payload
                except JSONDecodeError:
                    logger.warning(f"Invalid JSON response from classify \n {response.content}")
                    continue


if __name__ == "__main__":
    cli()

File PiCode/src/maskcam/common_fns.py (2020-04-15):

from maskcam.camera import Camera, image_to_base64
from requests.adapters import HTTPAdapter
from urllib3.util.retry import Retry
from requests import Session
from logging import DEBUG, INFO, WARNING, ERROR, CRITICAL
from logging import basicConfig, getLogger
import RPi.GPIO as GPIO
from json import dumps
from time import sleep
from attentive import quitevent
from threading import Thread
from base64 import b64encode
import pytz
from datetime import datetime
from .settings import NO_MASK_THRESHOLD, PERSON_PERCENTAGE

logger = getLogger(__name__)


def get_serial_number():
    # Get the rpis serial number
    try:
        with open('/proc/cpuinfo', 'r') as fp:
            for line in fp:
                if line[0:6] == "Serial":
                    cpuserial = line[10:26]
                    return cpuserial
    except:
        cpuserial = "ERROR000000000"
        return cpuserial


serial = get_serial_number()


def generate_payload(config, image, override='False'):
    data = dict(photo_data=image_to_base64(image),
                timestamp=datetime.utcnow().replace(tzinfo=pytz.utc).isoformat(),
                person_threshold=PERSON_PERCENTAGE(), mask_threshold=100 - NO_MASK_THRESHOLD(),
                device_serial=serial, override=override)
    return data


class Pinger():
    def __init__(self, gateway_URL, device_name):
        self.__stop = False
        self.gateway_url = gateway_URL
        self.session = session_with_retry_policy()
        self.thread = Thread(target=self.continue_until_stopped)
        self.serial = get_serial_number()
        self.device_name = device_name

    def stop(self):
        self.__stop = True

    def continue_until_stopped(self):
        while not quitevent.is_set():
            if self.__stop:
                break
            try:
                self.session.post(self.gateway_url,
                                  data=dumps(dict(device_serial=self.serial, device_name=self.device_name)))
                sleep(30)
            except Exception as e:
                logger.debug(f"Error code {e} while pinging")
                sleep(30)

    def start(self):
        self.thread.start()


def data_generator(Cam, threshold):
    images = []
    last_image = 0
    with Cam:
        # start getting images in a background thread
        # pre fill array
        images.append(Cam.read_frame())
        images.append(Cam.read_frame())
        # While we don't sigkill

        while not quitevent.is_set():
            if Cam.updated:
                images[last_image] = Cam.read_frame()
                # Sanity check that we have two images.
                if len(images) > 1:
                    threshold_percentage = Cam.compare_frames(images[0], images[1])
                    if threshold_percentage > threshold:
                        yield images[last_image]
                # rotate frames
                if last_image == 0:
                    last_image = 1
                else:
                    last_image = 0


def session_with_retry_policy() -> Session:
    http = Session()
    retry_strategy = Retry(
        total=5,
        status_forcelist=[500, 502, 503, 504],
        method_whitelist=["POST"],
        backoff_factor=3
    )
    adaptor = HTTPAdapter(max_retries=retry_strategy)
    http.adapters = {"https://": adaptor, "http://": adaptor}
    return http


def set_verbosity(verbose: int):
    log_int = {'4': DEBUG, '3': INFO, '2': WARNING, '1': ERROR, '0': CRITICAL}
    # The most verbose you can go is debug
    if verbose > len(log_int):
        basicConfig(level=DEBUG)
    else:
        if str(verbose) not in log_int.keys():
            raise ValueError(f"Invalid log level {verbose}")
        basicConfig(level=log_int[str(verbose)])
    # get some chatty logs to chill for a bit.
    getLogger("PIL").setLevel(WARNING)
    getLogger("boto3").setLevel(WARNING)
    # URLLIB gets way too chatty
    if verbose > 4:
        getLogger("urllib3").setLevel(DEBUG)
    else:
        getLogger("urllib3").setLevel(INFO)


def open_door(config, override=False):
    if override:
        logger.debug("Door triggered over by override. Uploading")
    pin = config.door_pin
    open_time = config.open_time

    GPIO.output(pin, 1)
    sleep(open_time)
    logger.debug(f"Door closing")
    GPIO.output(pin, 0)
    # if its an override we also need to send image.
    if override:
        with session_with_retry_policy() as Session:
            try:
                image = None
                while image is None:
                    image = config.camera.read_frame()

                data = dumps(generate_payload(config, image, override="True"))
                response = Session.post(url=f"{config.api_gateway}/upload",
                             data=data)
                logger.debug(response.json())
            except Exception as e:
                logger.debug(e)
                logger.warning(f"Something went wrong when trying to send override {pin}. Check debug log.")

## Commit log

2020-03-31 Implement camera view
2020-04-11 Calculate overall stats based on cameras
2020-04-12 Make confirm button smaller
2020-04-12 Implement front-end part for confirm button
2020-04-13 Implement confirmation button
2020-04-15 Implement refresh button
2020-04-15 Implement refresh button to reload activities
2020-04-15 Add PI code and lambdas
    [Connections.fzz]
2020-04-15 Set up README
    [Connections.fzz]
